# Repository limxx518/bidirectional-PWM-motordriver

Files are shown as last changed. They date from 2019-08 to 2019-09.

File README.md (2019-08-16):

# bidirectional-PWM-motordriver #
Test fixture to drive motors back and forth

## Hardware
4 layer PCB with dual input polarity and overvoltage shunting feature

## Software
User can select between center or edge aligned PWM along with configuring these parameters:
- Frequency from 10 to 100 Hz 
 - Duty cycle from 0 to 100
 - Direction CW, CCW or both
 - Deadtime
 - Number of cycles to run
 - Half-cycle duration
 
 ## Usage
 This board is meant to be used together with a serial terminal and USB to serial cable. Enter x/X anytime to restart program execution.
        
 ## Completed Board:
 


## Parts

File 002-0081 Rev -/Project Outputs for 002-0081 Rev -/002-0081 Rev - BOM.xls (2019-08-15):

PEM Part Number | Designator | Quantity
EE-1293 | C1 | 1
EE-1659 | C2 | 1
EE-1343 | C3 | 1
EE-1425 | C4, C7, C8, C13 | 4
EE-1708 | C5 | 1
EE-1981 | C6 | 1
EE-1661 | C9, C11 | 2
EE-1673 | C10 | 1
EE-1725 | C12 | 1
EE-1290 | D1 | 1
EE-1681 | D2, D3, D11 | 3
EE-2167 | D4, D5, D9, D10 | 4
EE-2166 | D6, D7, D12, D13, D14 | 5
EE-1946 | D8 | 1
EE-1116 | J1 | 1
EE-1855 | P1 | 1
EE-1879 | Q1, Q2 | 2
EE-1898 | Q3, Q6, Q7, Q8, Q11 | 5
EE-2053 | Q4, Q5 | 2
EE-1830 | Q9, Q10 | 2
EE-2066 | R1 | 1
EE-1296 | R2, R3, R9, R12, R15, R16, R17, R18, R20 | 9
EE-1295 | R4 | 1
EE-1297 | R5, R6 | 2
EE-1730 | R7, R10 | 2
EE-1238 | R8 | 1
EE-1581 | R11 | 1
EE-1798 | R13, R14 | 2
EE-1588 | R19, R21 | 2
EE-1900 | U1 | 1
EE-1248 | U2 | 1
EE-1655 | U3 | 1
EE-2165 | U4 | 1
EE-1801 | U5 | 1

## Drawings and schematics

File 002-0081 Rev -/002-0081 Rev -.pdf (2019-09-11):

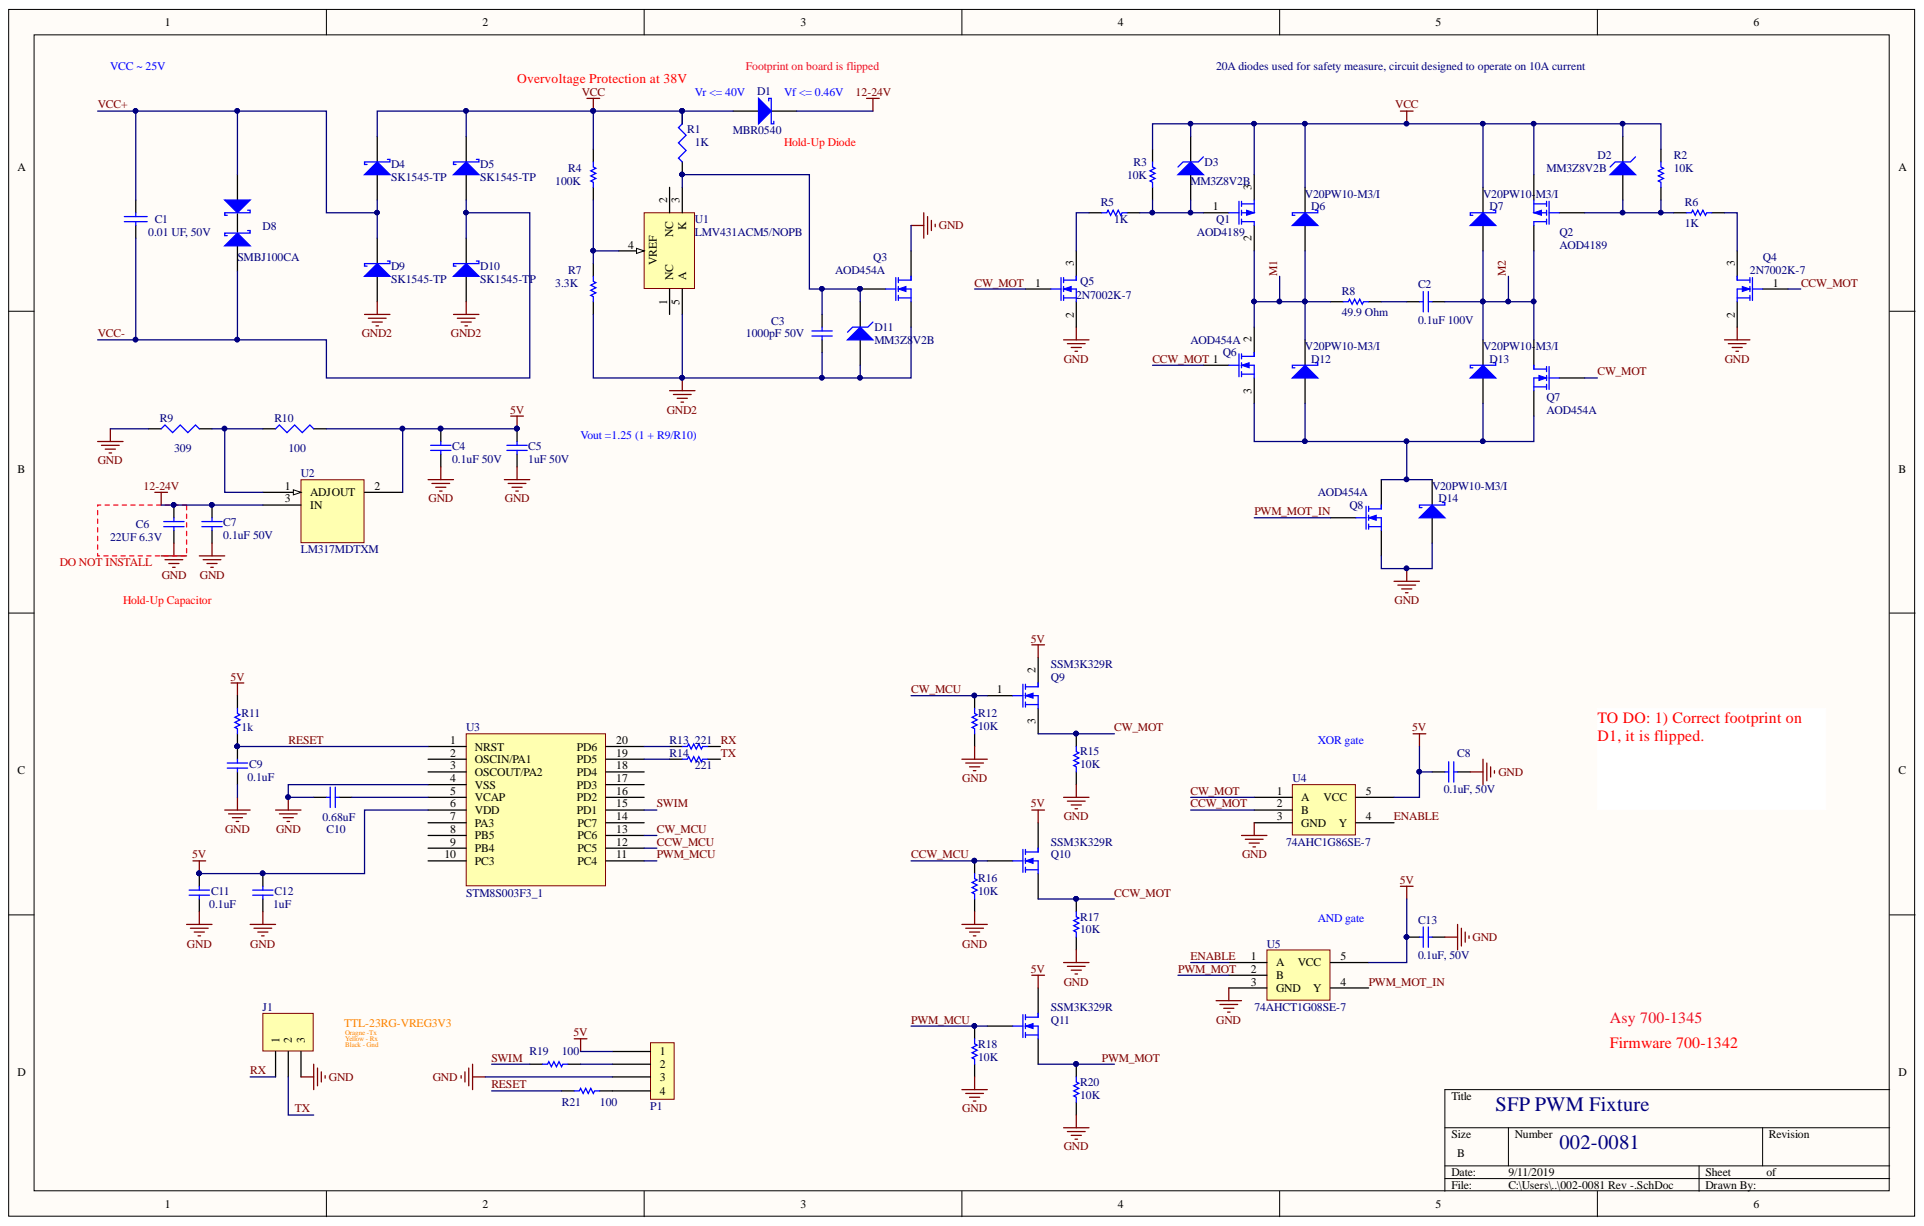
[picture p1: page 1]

Footprint on board is flipped

20A diodes used for safety measure, circuit designed to operate on 10A current

TO DO: 1) Correct footprint on
D1, it is flipped.

TTL-23RG-VREG3V3 Oragne -Tx Yellow - Rx Black - Gnd

Size B | Number 002-0081 | Revision

Date: 9/11/2019 | Sheet of
File: C:\Users\..\002-0081 Rev -.SchDoc | Drawn By:

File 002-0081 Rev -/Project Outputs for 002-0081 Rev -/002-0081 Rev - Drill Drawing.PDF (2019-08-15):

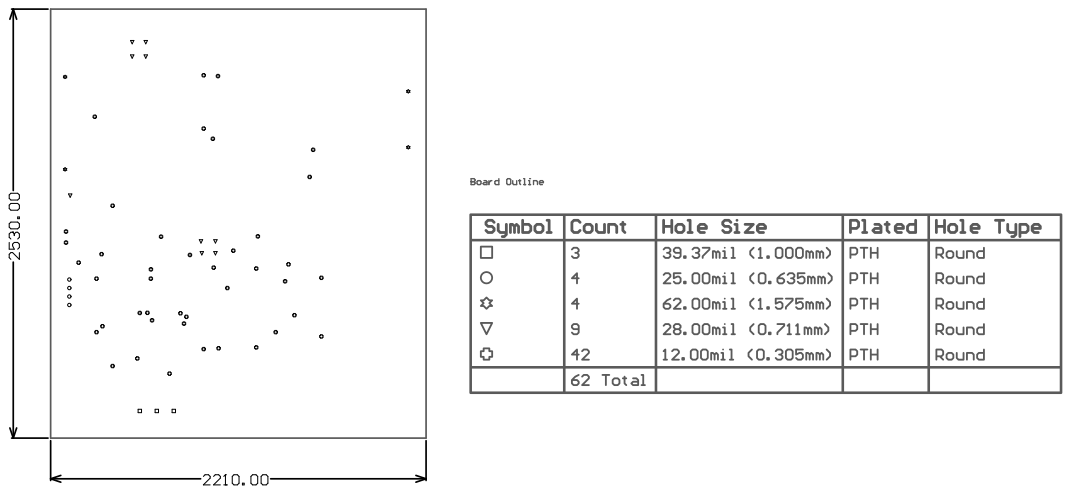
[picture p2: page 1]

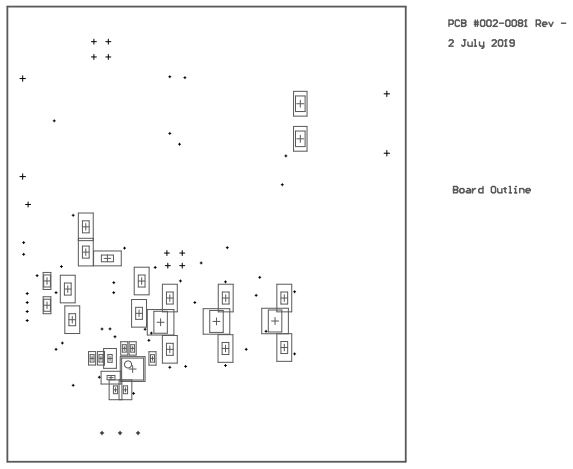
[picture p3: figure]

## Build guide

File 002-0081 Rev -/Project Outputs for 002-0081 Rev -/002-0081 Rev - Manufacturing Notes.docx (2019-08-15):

002-0081 Rev – Manufacturing Notes:

1) PCB
a. 0.062” thick
b. Copper on 4 layers.
c. Plated through holes
d. All layers to be 1 oz copper.
2) All hole dimensions apply after plating
a. <= +/-0.003 inches.
3) All plated through holes to have a minimum copper thickness
a. 0.001 inch.
4) Layer to Layer registration shall be
a. <=0.003 inches of true position.
5) Apply solder mask over bare copper both sides.
a. Solder mask to be LPI
b. Color transparent green.
c. Exposed conductive surfaces to be covered by (ROHS compliant) Immersion.
i. Gold (or)
ii. Silver (or)
iii. ENEPIG
6) Silkscreen component & solder side using
a. White epoxy.
b. Ensure epoxy does not bleed to exposed metal.
c. Silkscreen on both sides if comports are on both sides.
7) Fabricate in accordance with IPC-6011 & 6012, Class 2.
8) Board shall meet requirements of UL796 with a flammability of 94V-0.
a. UL Logo shall be located on PCB.
9) Outline dimensions are
a. +/-0.010 unless otherwise noted.
10) Remove all burrs and sharp edges.
11) Mechanical Layer 2 of Gerber is PCB Outline.
12) Layer Stack order:

.GTL

.G1

.G2

.GBL

Notes: Contact Jim Blesener 763-398-0456 x2102 (jimb@powerengmfg.com) with questions.

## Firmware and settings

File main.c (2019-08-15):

#define MAIN 1

#include <stdio.h>
#include <stdlib.h>
#include <string.h>
#include "stm8s.h"
#include "stm8s_gpio.h"
#include "stm8s_tim2.h"
#include "stm8s_uart1.h"
#include "stm8s_iwdg.h"
#include "stm8s_clk.h"
#include "stm8s_rst.h"
#include "stm8s_tim1.h"
#include "stm8s_it.h"
#include "var.h"

          
 /*******************************************************************************************************
*	NAME:			main()
*
*	DESCRIPTION:	This function handles user entry of parameter inputs. Function coded using state machine approach
*                   and several infinite loops. Each infinite loop corresponds to a unique state, as indicated by the
*                   value of process_state variable. Infinite loop is used to wait for user input indefinitely. 
*                   There is only one way a loop is exited and that's when input is valid. User inputs are processed 
*                   using processCommand function that processes accordingly to each unique state. At any point in time
*                   when program is running, user can input x/X to halt execution and reset program.
*			
*	INPUTS:		    
*
*	OUTPUTS:	    
*
*	Notes:          
*
*	CHANGES:
*	REF NO		DATE		WHO		DETAIL
*
****************************************************************************************/

void main(void)
{
    init();

    LOOP1:printOptions();
    while(1)
    {
        IWDG->KR = 0xAA;
        if(input_flag == INPUT_RECEIVED) 
            processCommand();
        else if(input_flag == INPUT_INVALID) 
        {
            printf("Error:Invalid Input\r");
            printf("\r");
            printOptions();
            input_flag = IDLE;                         //Idle state is needed to avoid repeatedly printing options
        }
        else if(input_flag == INPUT_VALID) 
        {
            input_flag = IDLE;
            printf("Enter frequency, duty and cycles\r");
            break;
        }
    }

    LOOP2: while(1)
    {
        IWDG->KR = 0xAA;
        if(input_flag == INPUT_RECEIVED) 
            processCommand();
        else if(input_flag == INPUT_INVALID)
        {
            printf("Error:Invalid Input\r");
            printf("\r");
            while(delay--);
            delay = DELAY_TIME;
            printf("Enter frequency, duty and cycles\r");
            input_flag = IDLE;
        }
        else if(input_flag == CANCEL_STATE) 
        {
            input_flag = IDLE;
            process_state = INPUT_STATE;
            init();
            goto LOOP1;
        }
        else if(input_flag == INPUT_VALID) 
        {
            init_PWM();
            
            //This block of code for debugging purposes
            printf("PRE: %u\r", prescaler);
            while(delay--);                     //delay needed to make sure whole msg printed without buffer overrun
            delay = DELAY_TIME;
            printf("ARR: %u\r", ARR);
            printf("Duty: %u\r", pulseWidth);
            while(delay--);
            delay = DELAY_TIME;
            printf("\r");
        
            input_flag = IDLE;
            printf("Enter cycle duration(ms), neutral time(ms) and direction(1(CW)/2(CCW)/3(Both))\r");
            break;
        }
    }  

    LOOP3: while(1)
    {
        IWDG->KR = 0xAA;
        if(input_flag == INPUT_RECEIVED)
            processCommand();
        else if(input_flag == CANCEL_STATE)
        {
            input_flag = IDLE;
            process_state = INPUT_STATE;
            init();
            goto LOOP1;
        }
        else if(input_flag == INPUT_INVALID)
        {
            input_flag = IDLE;
            printf("Error:Invalid Input\r");
            printf("\r");
            while(delay--);
            delay = DELAY_TIME;
            printf("Enter cycle duration(ms), neutral time(ms) and direction(1(CW)/2(CCW)/3(Both))\r");
        }
        else if(input_flag == INPUT_VALID)
        {
            input_flag = IDLE;
            printf("Enter s/S to start\r");
        break;
        }
    }
            
    LOOP4: while(1)
    {
        IWDG->KR = 0xAA;
        if(input_flag == INPUT_RECEIVED) 
            processCommand();
        else if(input_flag == CANCEL_STATE) 
        {
            input_flag = IDLE;
            process_state = INPUT_STATE;
            init();
            goto LOOP1;
        }
        else if(input_flag == INPUT_INVALID)
        {
            printf("Error:Invalid Input\r");
            printf("\r");
            printf("Hit s/S to start\r");
            input_flag = IDLE;
        }
        else if(input_flag == INPUT_VALID)
        {
            input_flag = IDLE;
            TIM1_Cmd(ENABLE);
            TIM2_Cmd(ENABLE);
            break;
        }
    }
    
    LOOP5: while(1)
    {
        IWDG->KR = 0xAA;
        if(input_flag == INPUT_RECEIVED) processCommand();
        else if(input_flag == CANCEL_STATE) 
        {
            input_flag = IDLE;
            process_state = INPUT_STATE;
            init();
            goto LOOP1;
        }
        else if(print_flag)
        {
            print_flag = 0;
            printf("Cycle count: %lu\r", cycle_count);
            printf("Direction: %s\r",  half_cycle_flag ? "CCW":"CW");            
            printf("\r");  
            if(cycle_count == PWM_ints[COUNT])
            {
                if(PWM_ints[DIR]==3 && half_cycle_flag) while(delay--);
                else if(PWM_ints[DIR] == 1 || PWM_ints[DIR] == 2) while(delay--);
            }
        }
    }
}

/*******************************************************************************************************
*	NAME:			void printOptions(void)
*
*	DESCRIPTION:	This function prints the first block of input choices upon program startup or reset
*			
*	INPUTS:		    
*
*	OUTPUTS:	    
*
*	Notes:          
*
*	CHANGES:
*	REF NO		DATE		WHO		DETAIL
*
****************************************************************************************/
void printOptions(void)
{
    printf("Select test mode(enter number of selection):\r");
    printf("1: Edge-aligned PWM\r");
    printf("2: Center-aligned PWM\r");
    //printf("3: One-pulse mode\r");
}


/*******************************************************************************************************
*	NAME:			void processCommand(void)
*
*	DESCRIPTION:	This function is called from each infinite loop in main() when input is received. processComand
*                   sets the value of input_flag to be valid, invalid or a cancel state for the loop to 
*                   process subsequently
*			
*	INPUTS:		    
*
*	OUTPUTS:	    
*
*	Notes:          
*
*	CHANGES:
*	REF NO		DATE		WHO		DETAIL
*
****************************************************************************************/
void processCommand(void)
{
    //First block processes Options command
    if(process_state == INPUT_STATE)
    {
        if(strncmp("1",rx_buff, 1) == 0) input_mode = 0x01;
        else if (strncmp("2",rx_buff, 1) == 0) input_mode = 0x02;
        else if (strncmp("3",rx_buff, 1) == 0) input_mode = 0x03;
        else 
            input_flag = INPUT_INVALID;
        if(input_flag != INPUT_INVALID)
        {
            input_flag = INPUT_VALID;
            process_state = PARAM_STATE_1;
        }
    }
    
    //Second block processes 1st block of parameters
    else if(process_state == PARAM_STATE_1)
    {
        uint8_t ind;
        if(strncmp("X", rx_buff, 1) == 0) 
        {
            input_flag = CANCEL_STATE; 
            return;
        }
        ind = parseString(rx_buff);
        if(ind)
        {
            input_flag = INPUT_VALID;
            process_state = PARAM_STATE_2;
        }            
        else 
        {
            input_flag = INPUT_INVALID;
            PWM_params_index = 0;
        }
    }
    
    //Third block processes 2nd block of parameters
    else if(process_state == PARAM_STATE_2)
    {
        uint8_t ind;
        if(strncmp("X", rx_buff, 1) == 0) 
        {
            input_flag = CANCEL_STATE; 
            return;
        }
        ind = parseString(rx_buff);
        if(ind)
        {
            input_flag = INPUT_VALID;
            process_state = WAIT_FOR_START;
        }            
        else 
        {
            input_flag = INPUT_INVALID;
            PWM_params_index = 3;
        }
    }

    //Fourth block processes Start command
    else if(process_state == WAIT_FOR_START)
    {
        if(strncmp("S", rx_buff, 1) == 0)
        {
            input_flag = INPUT_VALID;
            process_state = RUNNING_STATE;
        }
        else if(strncmp("X", rx_buff, 1) == 0)  input_flag = CANCEL_STATE;    
        else 
            input_flag = INPUT_INVALID;
    } 
    
    else if(process_state == RUNNING_STATE)
    {
        if(strncmp("X", rx_buff, 1) == 0) input_flag = CANCEL_STATE;     
        else 
            input_flag = IDLE;
    }
}


/*******************************************************************************************************
*	NAME:			uint8_t parseString(char *str)
*
*	DESCRIPTION:	This function is called from the processCommand function to process parameter input strings
*                   entered by user. This function also does parameter checking and returns 0 if there's an error, 
*                   1 otherwise. Those return values will be subsequently processed by the processCommand function.
*			
*	INPUTS:	        (char*) str	    
*
*	OUTPUTS:	    uint8_t, 1 or 0
*
*	Notes:          
*
*	CHANGES:
*	REF NO		DATE		WHO		DETAIL
*
****************************************************************************************/		
uint8_t parseString(char *str)
{
    unsigned long test;
    uint8_t *ptr;
    uint8_t i,j;

    //This block separates the string to separate integer strings
    uint8_t *pch;
    //uint8_t *copy = (uint8_t *)malloc((strlen(str) + 1) * sizeof(uint8_t));
    uint8_t copy[25] = {0x00};
    //For some reason, malloc pointer wasn't successful, yet to determine why
    //~ i = (uint8_t)strlen(str);
    //~ copy = (uint8_t*)malloc((i+1) * sizeof(uint8_t));
    //~ printf("String length is %u\r", strlen(str));
    //~ printf("copy address is %x\r", &copy);
    //~ printf("copy is pointing to %s\r", copy);
    strcpy(copy, str);
    pch = strtok(copy, ",");
    while(pch != NULL && (PWM_params_index < 6))
    {
        strcpy(PWM_params[PWM_params_index++], pch);
        //printf("Copied string: %s\r", PWM_params[PWM_params_index++]);
        pch = strtok(NULL, ",");
    }
    
    //free(copy);

    //These two statements are to check if user input all required parameters
    if(process_state == PARAM_STATE_1 && PWM_params_index != 3) return 0x00;
    else if(process_state == PARAM_STATE_2 && PWM_params_index != 6) return 0x00;
    
    //This block converts the integer strings to integers and performs validations
    i = (process_state == PARAM_STATE_1) ? 0x00: 0x03;
    j = i;
    while( i < (j+3) )
    {
        test = strtoul(PWM_params[i], &ptr, 10);
        if(test) 
        {
            switch(i){
            case 0: if(test >= 10 && test <= 10000) PWM_ints[i] = (uint32_t)test;
                    else return 0x00;
                    break;
            case 1: if(test <= 100) PWM_ints[i] = (uint32_t)test;
                    else return 0x00;
                    break;
            case 2: if(!test) return 0x00;
                    else PWM_ints[i] = (uint32_t)test;
                    break;
            case 3: if(!test) return 0x00;
                    else PWM_ints[i] = (uint32_t)test;
                    break;
            case 5: if(test >= 1 && test <= 3) PWM_ints[i] = (uint32_t)test;
                    else return 0x00;
                    break;
            default: PWM_ints[i] = (uint32_t)test;
            }
        }
        else if(i == 1) PWM_ints[i] = 0;     //0 duty cycle is possible
        else if(i == 4) PWM_ints[i] = 0;     //0 neutral time is possible
        else return 0x00;      //fail
        i++;
    }
    return 0x01;            //success
}


/********************************************************************************************
* Name:				int putchar(const char c)
*
* Description:	 	This code section is called from printf		
*
* Inputs			a character to place on the xmit buffer
*
* Outputs			updated xmit_buff
*		
* Process			- We can never stall the system waiting for transmit
*					- We load data into the xmit buffer and index the head counter
*					- The isr increments the tail counter when running
*					- This section increments the tail counter when we start the isr for a new xmit
*					- If the head and tail are = we are not xmitting anything and ISR is off - ISR does this
*					- We have set the xmit_buff to a length of TX_BUFF_SIZE
*						* if we use multiple prints that overrun the buffer we wrap over our xmit buffer
*							We do not stall and wait for the xmit to catch up 
*					
* Note:			    - The STM8S MCU doesn't have UART0, so we can't disable printf using UART0 in project properties.
*                   - In order to force printf to use io_putchar, we have to follow the declaration of putchar function in stdio.h
*                   - putchar() must return 1, otherwise printf() will stop after first character
*                   - The information is taken from Raisonance ST7/STM8 Compiler manual, document version 01/25/2011
*
* Changes:			Date			Who			Detail
*					
********************************************************************************************/
int putchar(const char c)
{
    // move this character to the buffer -- we need to halt the isr interrupt to ensure we do not reindex in process
	_sim_();												// disable isr - ensure index is changed as load character to buffer

    // load the latest char
    xmit_buff[xmit_buff_head++] = (char)c;					// load the newest character
     
    // when the buffer has indexed to the end wrap to the beginning
	if (xmit_buff_head >= TX_BUFF_SIZE)				    	// we can only dump to end of buffer and then wrap back to 0
		xmit_buff_head = 0;									// loop back to 0
	_rim_();												// enable isr


	// If we are not sending rs232 then start the sending by initialing isr.
	if (xmit_buff_sending_flag == RESET)					// not sending anything so start sending
	{
		xmit_buff_sending_flag = SET;						// turn on the sending flag
		UART1_SendData8(xmit_buff[xmit_buff_tail++]);       // just send a normal character like ISR would have sent it
		UART1->CR2 = 0b10101100;			                // TIEN = 1 (bit 7), enable TX interrupt
		if(xmit_buff_tail >= TX_BUFF_SIZE)				    // increment to next char to send
			xmit_buff_tail = 0;								// loop back to 0
	}

    return(1);
}   

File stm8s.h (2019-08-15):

/**
  ******************************************************************************
  * @file    stm8s.h
  * @author  MCD Application Team
  * @version V2.1.0
  * @date    18-November-2011
  * @brief   This file contains all HW registers definitions and memory mapping.
  ******************************************************************************
  * @attention
  *
  * THE PRESENT FIRMWARE WHICH IS FOR GUIDANCE ONLY AIMS AT PROVIDING CUSTOMERS
  * WITH CODING INFORMATION REGARDING THEIR PRODUCTS IN ORDER FOR THEM TO SAVE
  * TIME. AS A RESULT, STMICROELECTRONICS SHALL NOT BE HELD LIABLE FOR ANY
  * DIRECT, INDIRECT OR CONSEQUENTIAL DAMAGES WITH RESPECT TO ANY CLAIMS ARISING
  * FROM THE CONTENT OF SUCH FIRMWARE AND/OR THE USE MADE BY CUSTOMERS OF THE
  * CODING INFORMATION CONTAINED HEREIN IN CONNECTION WITH THEIR PRODUCTS.
  *
  * <h2><center>&copy; COPYRIGHT 2011 STMicroelectronics</center></h2>
  ******************************************************************************
  */

/* Define to prevent recursive inclusion -------------------------------------*/
#ifndef __STM8S_H
#define __STM8S_H

/** @addtogroup STM8S_StdPeriph_Driver
  * @{
  */
  
/* Uncomment the line below according to the target STM8S or STM8A device used in your
   application. */

 /* #define STM8S208 */      /*!< STM8S High density devices with CAN */
 /* #define STM8S207 */      /*!< STM8S High density devices without CAN */
 /* #define STM8S007 */      /*!< STM8S Value Line High density devices */
 /* #define STM8AF52Ax */    /*!< STM8A High density devices with CAN */
 /* #define STM8AF62Ax */    /*!< STM8A High density devices without CAN */
 /* #define STM8S105 */      /*!< STM8S Medium density devices */
 /* #define STM8S005 */      /*!< STM8S Value Line Medium density devices */
 /* #define STM8AF626x */    /*!< STM8A Medium density devices */
 /* #define STM8S103 */      /*!< STM8S Low density devices */
 #define STM8S003            /*!< STM8S Value Line Low density devices */
 /* #define STM8S903 */      /*!< STM8S Low density devices */

/*   Tip: To avoid modifying this file each time you need to switch between these
        devices, you can define the device in your toolchain compiler preprocessor. 

  - High-Density STM8A devices are the STM8AF52xx STM8AF6269/8x/Ax,
    STM8AF51xx, and STM8AF6169/7x/8x/9x/Ax microcontrollers where the Flash memory
    density ranges between 32 to 128 Kbytes
  - Medium-Density STM8A devices are the STM8AF622x/4x, STM8AF6266/68,
    STM8AF612x/4x, and STM8AF6166/68 microcontrollers where the Flash memory 
    density ranges between 8 to 32 Kbytes
  - High-Density STM8S devices are the STM8S207xx, STM8S007 and STM8S208xx microcontrollers
    where the Flash memory density ranges between 32 to 128 Kbytes.
  - Medium-Density STM8S devices are the STM8S105x and STM8S005 microcontrollers
    where the Flash memory density ranges between 16 to 32-Kbytes.
  - Low-Density STM8S devices are the STM8S103xx, STM8S003 and STM8S903xx microcontrollers
    where the Flash density is 8 Kbytes. */

#if !defined (STM8S208) && !defined (STM8S207) && !defined (STM8S105) && \
    !defined (STM8S103) && !defined (STM8S903) && !defined (STM8AF52Ax) && \
    !defined (STM8AF62Ax) && !defined (STM8AF626x) && !defined (STM8S007) && \
    !defined (STM8S003)&& !defined (STM8S005) 
 #error "Please select first the target STM8S/A device used in your application (in stm8s.h file)"
#endif

/******************************************************************************/
/*                   Library configuration section                            */
/******************************************************************************/
/* Check the used compiler */
#if defined(__CSMC__)
 #define _COSMIC_
#elif defined(__RCST7__)
 #define _RAISONANCE_
#elif defined(__ICCSTM8__)
 #define _IAR_
#else
 #error "Unsupported Compiler!"          /* Compiler defines not found */
#endif

#if !defined  USE_STDPERIPH_DRIVER
/* Comment the line below if you will not use the peripherals drivers.
   In this case, these drivers will not be included and the application code will be
   based on direct access to peripherals registers */
 #define USE_STDPERIPH_DRIVER
#endif

/**
  * @brief  In the following line adjust the value of External High Speed oscillator (HSE)
   used in your application

   Tip: To avoid modifying this file each time you need to use different HSE, you
        can define the HSE value in your toolchain compiler preprocessor.
  */
#if !defined  HSE_Value
 #if defined (STM8S208) || defined (STM8S207) || defined (STM8S007) || defined (STM8AF52Ax) || \
     defined (STM8AF62Ax)
  #define HSE_VALUE ((u32)24000000) /* Value of the External oscillator in Hz*/
 #else
  #define HSE_VALUE ((u32)16000000) /* Value of the External oscillator in Hz*/
 #endif /* STM8S208 || STM8S207 || STM8S007 || STM8AF62Ax || STM8AF52Ax */
#endif /* HSE_Value */

/**
  * @brief  Definition of Device on-chip RC oscillator frequencies
  */
#define HSI_VALUE   ((uint32_t)16000000) /*!< Typical Value of the HSI in Hz */
#define LSI_VALUE   ((uint32_t)128000)   /*!< Typical Value of the LSI in Hz */

#ifdef _COSMIC_
 #define FAR  @far
 #define NEAR @near
 #define TINY @tiny
 #define EEPROM @eeprom
 #define CONST  const
#elif defined (_RAISONANCE_) /* __RCST7__ */
 #define FAR  far
 #define NEAR data
 #define TINY page0
 #define EEPROM eeprom
 #define CONST  code
 #if defined (STM8S208) || defined (STM8S207) || defined (STM8S007) || defined (STM8AF52Ax) || \
     defined (STM8AF62Ax)
   /*!< Used with memory Models for code higher than 64K */
  #define MEMCPY fmemcpy
 #else /* STM8S903, STM8S103, STM8S003, STM8S105, STM8AF626x */
  /*!< Used with memory Models for code less than 64K */
  #define MEMCPY memcpy
 #endif /* STM8S208 or STM8S207 or STM8S007 or STM8AF62Ax or STM8AF52Ax */ 
#else /*_IAR_*/
 #define FAR  __far
 #define NEAR __near
 #define TINY __tiny
 #define EEPROM __eeprom
 #define CONST  const
#endif /* __CSMC__ */

/* For FLASH routines, select whether pointer will be declared as near (2 bytes,
   to handle code smaller than 64KB) or far (3 bytes, to handle code larger 
   than 64K) */

#if defined (STM8S105) || defined (STM8S005) || defined (STM8S103) || defined (STM8S003) || \
    defined (STM8S903) || defined (STM8AF626x)
/*!< Used with memory Models for code smaller than 64K */
 #define PointerAttr NEAR
 #define MemoryAddressCast uint16_t
#else /* STM8S208 or STM8S207 or STM8AF62Ax or STM8AF52Ax */
/*!< Used with memory Models for code higher than 64K */
 #define PointerAttr FAR
 #define MemoryAddressCast uint32_t
#endif /* STM8S105 or STM8S103 or STM8S003 or STM8S903 or STM8AF626x */

/* Uncomment the line below to enable the FLASH functions execution from RAM */
#if !defined (RAM_EXECUTION)
/* #define RAM_EXECUTION  (1) */
#endif /* RAM_EXECUTION */
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

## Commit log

2019-08-15 Altium files
    [002-0081 Rev - BOM.xls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]
2019-09-11 Added board schematic pdf

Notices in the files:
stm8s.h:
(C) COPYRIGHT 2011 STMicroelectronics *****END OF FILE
